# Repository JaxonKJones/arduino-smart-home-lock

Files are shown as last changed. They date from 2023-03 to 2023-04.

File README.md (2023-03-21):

# Project Description
This project was designed for home and apartment renters that want an affordable smart lock that is compliant with renter restrictions on changing locks (although anyone is welcome to use it). This is accomplished by utilizing existing lock hardware and keeping the keyed entry free for use. This design is compatible with most kinds of door locks and was made to be "plug and play." If modifications are needed, the source files included in this repository can be modified to fit your door. Assembly instructions are available through [instructables.com](https://www.instructables.com/) (project not yet released).

This smart lock uses an Arduino Nano as the microcontroller. It interfaces with a real time clock (the DS3231) to handle all scheduled events. The Nano also interfaces with a HC-05 Bluetooth module for users to program scheduled events, and manually engage or disengage the lock. The circuit is battery operated and uses a rechargeable 3.7v 18650 battery that is boosted to 5v. 

The smart lock is accessible/programmable via a bluetooth terminal smartphone app like the one **[here](https://play.google.com/store/apps/details?id=de.kai_morich.serial_bluetooth_terminal&hl=en_US&gl=US)**. Upon connecting and providing appropriate credentials, a menu will be displayed for the user allowing you to select several options. The major features are listed below:

## Modes:
Scheduling Mode: This option lets the user add, delete, or view existing schedules. When the desired schedules have been set the circuit enters into low power mode and can only be awoken by programmed interrupts on the DS3231 or the on board switch. This mode uses the least power at approximately 1 mAh. Using this mode gives the user the longest battery life with around 140 days before needing to be recharged.  

Bluetooth Mode: This mode uses the most power and is not recommended but is available for convenience if desired. This mode keeps the module paired, or open to pairing, so that the deadbolt can be locked or unlocked at any moment

Bluetooth Limited Mode: This mode combines the functionality of the previous two modes. The user defines a schedule for when the module should be on and pairable. This helps reduce unnecessary battery usage for time when the lock state is least likely to change (e.g. sleeping hours, working hours, school hours, etc.) 

## Quick Facts:
**Major Components:**
- Arduino Nano
- DS3231 Real Time Clock
- HC-05 Bluetooth Module 
- MG-90 Servo
- 18650 Battery
<!-- Total Project Time: ~40 hours -->
**Total project cost:** $25 (Market equivalents of this project cost ~$100+)  
See [Bill of Materials](#bill-of-materials)

**Battery Life**
140 day battery life in schedule mode°  
30 day battery life in Bluetooth limited mode*°  
*Based on a 3500 mAh 18650 battery
°Based on a 12 hour availability

# Bill of Materials
**NOTE:** Buying these components online usually means you'll need to purchase a pack or 2+. I'd recommend first looking for a local source if you don't have these components already. If a local supplier is unreasonable then [Temu](https://www.temu.com/) or [AliExpress](https://www.aliexpress.us/?gatewayAdapt=glo2usa&_randl_shipto=US) are your cheapsest options and [Amazon](https://www.amazon.com/) or [Ebay](https://www.ebay.com/) are your fastest options.
- [Arduino Nano](https://www.temu.com/type-c-usb-nano-3-0-with-bootloader-compatible-nano-3-0-controller-for-arduino-ch340-usb-driver-16mhz-original-ic-atmega328p-g-601099512651761.h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)
- [HC-05 Bluetooth Module](https://www.ebay.com/itm/364130886349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)
- [DS3231 Real Time Clock](https://www.amazon.com/DS3231-AT24C32-Module-Memory-Replace/dp/B09LLMYBM1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)
- [Portable Battery Pack](https://www.ebay.com/itm/255619278468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)** 
- [MG90 Servo](https://www.temu.com/mg90s-metal-gear-digital-9g-servo-for-rc-helicopter-plane-boat-car-mg90-9g-g-601099512694957.html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)  
**If you can afford it, I'd recommend spending a bit more money to purchase a nice battery. Many cheap batteries on the internet lie about their capacity and you'll severally limit the battery life of the smart lock if you get a bad battery - could just buy a [case](https://www.aliexpress.us/item/3256802714206963.html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) or [this one](https://www.amazon.com/Diymore-Battery-Shield-Raspberry-Arduino/dp/B0784FPF8J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) (An 18650 battery case if important because it has a built in charing circuit and boost converter) and then get the [battery](https://www.18650batterystore.com/products/samsung-35e-protected) separtely to ensure you get a good product
- 2x MOSFET
- SPST Switch
- Momentary Switch
- 2x 10k ohm resistors
- 1x 2k ohm resistor
- 1x 4k ohm resistor
- 2x 330 microFarad Capacitor
- PCB - see pcb under [Systems](#systems)

# Instructions
Work in progress. Will be posted on instructables.com
<!-- finish... -->

# Systems
## Code
All of the code for this project is located in a single file called 
**arduino_smart_home_lock_code.ino** located in the arduino_smart_home_lock folder. This single file will contain all the functions needed for the arduino nano. If you are curious, I encourage you to read through the code to become familiar with it. There are also variables you may change such as the password to access the lock via bluetooth.
<!-- finish... -->

## PCB
The schematic and PCB for this project was created in Eagle - a software produced by autodesk. The PCB folder contains both a schematic (for reference and hand soldering) and a PCB file that can be manufactured by companies such as [jlcpcb](https://jlcpcb.com/) if you'd like to have a board that is professionally made. 

## Mechanical
The case for this smart lock can be 3D printed using any home 3D printer. All tolerances for fits have been adjusted for the ender 3 v2 but should work on any printer with equal or higher printing accuracy. Several versions of the case are available in the STL folder.
<!-- finish... -->

# Disclaimer
<!-- finish... -->

# Acknowledgements
Special thanks to the following individuals for providing critical support and feedback to make this project a success:  
Jarom Christensen   -   PCB design  
Devin Bingham       -   PCB debugging  
Michael Davis       -   Feature suggestions and market valuation  
My Wife             -   Letting me use our kitchen table as my workbench for 3 weeks

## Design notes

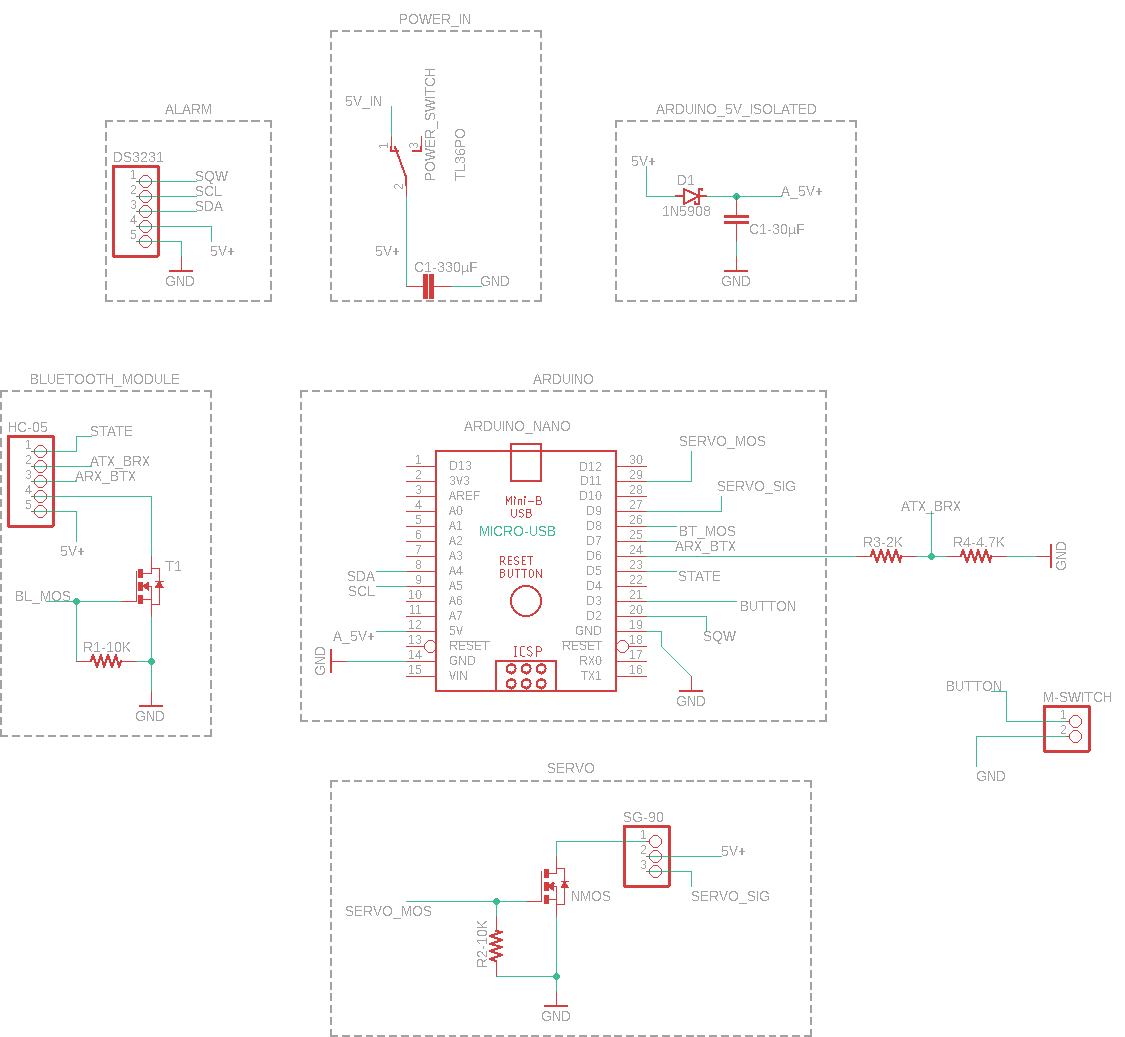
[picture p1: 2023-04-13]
Schematic and PCB/Wire Diagram.png

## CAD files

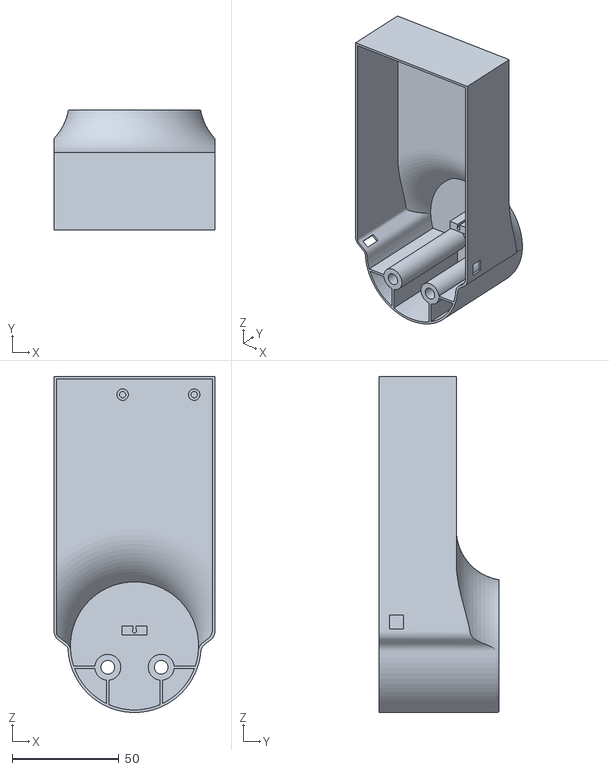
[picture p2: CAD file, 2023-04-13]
STL/Smart Home Lock Casing_Final - fully enclosed.stl
75.4 x 56.2 x 157.4

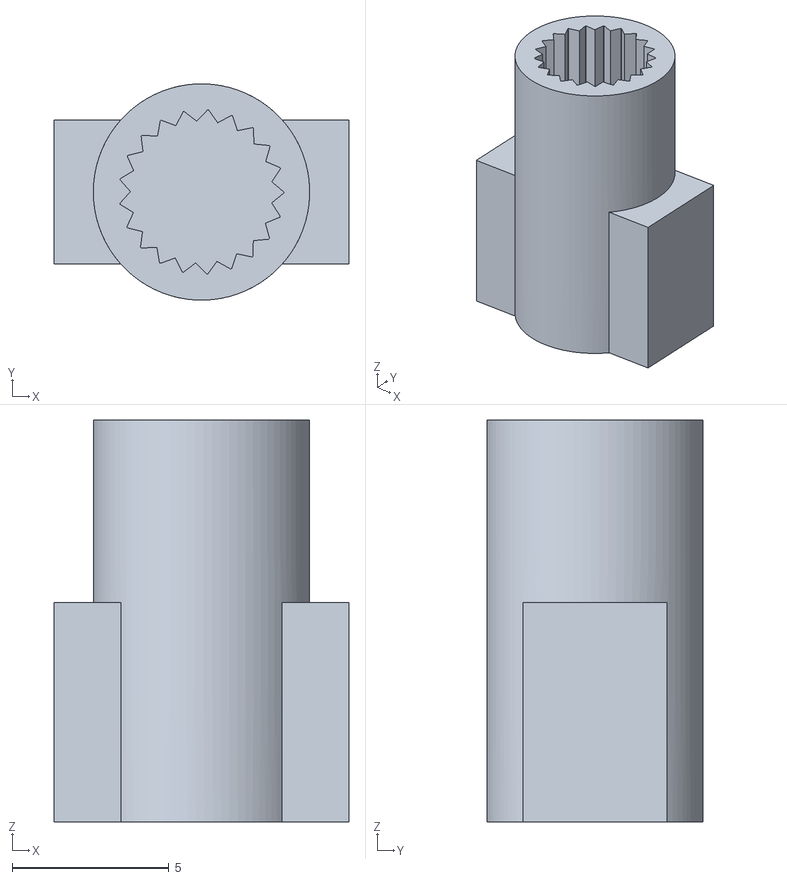
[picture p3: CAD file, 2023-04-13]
STL/SG90_Servo_Horn_Door_Lock.stl
9.40 x 6.90 x 12.8

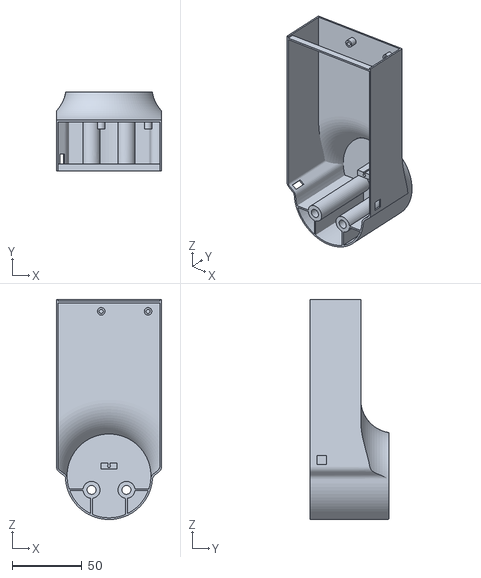
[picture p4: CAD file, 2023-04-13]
STL/Smart Home Lock Casing_Final - open top.stl
75.4 x 56.2 x 157.4

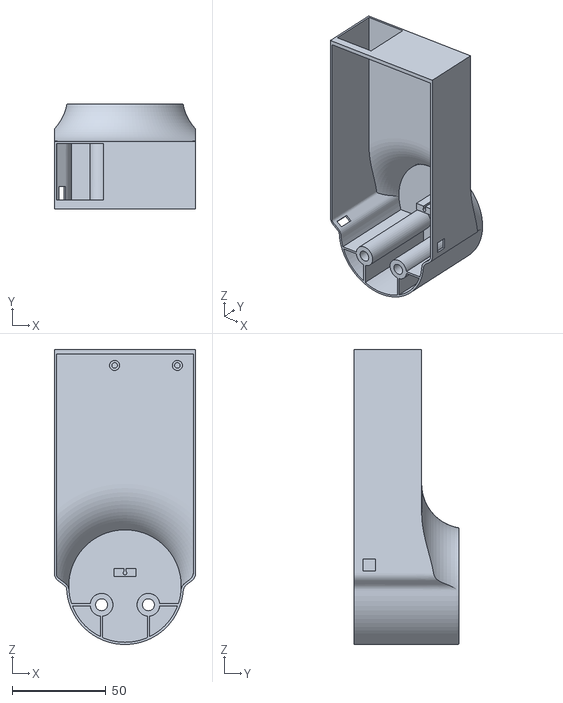
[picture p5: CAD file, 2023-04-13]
STL/Smart Home Lock Casing_Final - open battery port.stl
75.4 x 56.2 x 157.4

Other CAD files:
STL/SG90_Servo_Horn_Door_Lock.f3d
STL/Smart Home Lock Casing CAD.f3d

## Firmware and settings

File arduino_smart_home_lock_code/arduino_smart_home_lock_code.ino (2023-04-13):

#include <SoftwareSerial.h>
#include <avr/sleep.h>
#include <EEPROM.h>
#include <Wire.h>
#include "RTClib.h"
#include <Servo.h>


RTC_DS3231 rtc;
Servo lock;

#define STATE_PIN 5  // set state pin to pin 5
#define EN_PIN 4  // set enable pin to pin 4
#define BUTTON_PIN 3  // set button pin to pin 3
volatile bool fromButton = false;
volatile int buttonState = 0;
volatile long buttonCalls = 0;
#define ALARM_PIN 2 // interrupt pin from DS3231
#define BLUETOOTH_MOS 8 // mosfet for hc-05
#define SERVO 9 // pwm pin for servo
#define SERVO_MOS 11 // servo enable pin
SoftwareSerial BTserial(7, 6); // RX | TX

// User Variables
#define password "11235" //set your password here
#define verbose false //turn on when debugging from serial monitor, otherwise keep this false
#define TEST false //keep this false unless testing specific code in the test() function

// function declarations
void bprint(String arg);
void Fbprint(__FlashStringHelper* arg);
void auth();
int menu();
void pair(bool checkTimeOut);
void scheduler();
void save(char day, char h1, char h2, char m1, char m2, char state);
void del(int index);
char* load(bool print);
long nextEvent(char events[]);
void setAlarm(long);
void bluetoothMode();
void bluetoothLimited();
void scheduleMode();
void enterSleep();
void dev();
void servo(int state);
void vacationMode();
void buttonISR();
void alarmISR();


// setup function
void setup() { 
  // Serial Settings
  if(verbose) {
    Serial.begin(9600);
  }
  BTserial.begin(9600);
  Fbprint(F("Powering on..."));

  //rtc config
  Wire.begin();
  rtc.begin();
  // rtc.adjust(DateTime(F(__DATE__), F(__TIME__))); //Keep this commented out otherwise the RTC will reset anytime the arduino is powercycled
  pinMode(ALARM_PIN, INPUT_PULLUP);
  rtc.disableAlarm(1);
  rtc.disableAlarm(2);
  rtc.clearAlarm(1);
  rtc.clearAlarm(2);
  rtc.writeSqwPinMode(DS3231_OFF);
  rtc.disable32K();

  //servo config
  lock.attach(9);

  //pin config
  pinMode(STATE_PIN, INPUT);
  pinMode(BUTTON_PIN, INPUT_PULLUP);
  pinMode(BLUETOOTH_MOS, OUTPUT);
  digitalWrite(BLUETOOTH_MOS, HIGH);
  pinMode(EN_PIN, OUTPUT);
  digitalWrite(EN_PIN, LOW);
  pinMode(SERVO_MOS, OUTPUT);
  digitalWrite(SERVO_MOS, LOW);

  if(TEST == true){
    test();
  }

  //pair if not already connected
  if(digitalRead(STATE_PIN) == LOW){
    pair(true); // pair mode with timeout
  }
  auth();
}

// main loop
void loop() {
  int mode = menu();
  if (mode == '1'){
    //run scheduler
    scheduler();
  }
  if (mode == '2'){
    //run schedule mode
    scheduleMode();
  }
  else if (mode == '3'){
    //run bluetooth mode
    bluetoothMode();
  }
  else if (mode =='4'){
    //config bluetooth limited mode
    bluetoothLimited();
  }
  else if (mode == '5'){
    // run vacation mode
    vacationMode();
  }
  else if (mode == '6'){
    // run dev mode
    dev();
  }
}

void test(){
  Fbprint(F("Testing..."));
  // BTserial.print(F(\Testing...\n"));
  while(true){
    //test code here.
     char events[] = {'5', '1', '1', '1', '0', 'L','5', '1', '1', '1', '2', 'L','5', '1', '1', '1', '3', 'L','5', '1', '1', '1', '4', 'L', NULL};
    // char events[] = {'5', '1', '1', '0', '8', 'L'};
    long alarm = nextEvent(events);
    setAlarm(alarm);
    enterSleep();

    // delay(10000);
  }
}

// function definitions
void bprint(String arg) {
  if (verbose){
    Serial.println(arg);
  }
}

void Fbprint(__FlashStringHelper* arg) {
  if (verbose) {
    Serial.println(arg);
  }
}

void auth(){
  BTserial.print(F("\n-Home Lock-"));
  BTserial.print(F("\nEnter Password: "));
  long startTime = millis();
  // if user takes longer than 60s to enter password, it will go to scheduleMode
  while(true){
    if (BTserial.available()) {
      String input = BTserial.readString();
      delay(30);
      if (input == password){
        BTserial.print(F("\nAuthenticated..."));
        Fbprint(F("Authenticated..."));
        return;
      }
      else{
        BTserial.print(F("\nPassword Incorrect"));
      }
      // check to see if it has been 60s
      if (millis() - startTime > 60000){
        BTserial.print(F("\nTimed Out..."));
        scheduleMode();
      }
    }
  }
}

int menu(){
  if(digitalRead(STATE_PIN) == LOW){
    pair(false);
  }
  BTserial.print(F("\n\n-Main Menu-\n1: Scheduler\n2: Schedule Mode\n3: Bluetooth Mode\n4: Bluetooth Limited\n5: Vacation Mode\n6: Dev"));
  while(true){
    if (BTserial.available()) {
      char command = BTserial.read();
      if (command == '0') {
        return command;
      } 
      else if (command == '1') {
        return command;
      }
      else if (command == '2') {
        return command;
      }
      else if (command == '3') {
        return command;
      }
      else if (command == '4') {
        return command;
      }
      else if (command == '5') {
        return command;
      }
      else if (command == '6') {
        return command;
      }
      else if (command == '7') {
        return command;
      }
      else if (command == '8') {
        return command;
      }
      else if (command == '9') {
        return command;
      }
    }
    if (digitalRead(STATE_PIN) == LOW){
      pair(false);
    }
  }
    
}

void pair(bool checkTimeOut){
  Fbprint(F("Pairing..."));
  long startTime = millis();
  while(digitalRead(STATE_PIN) == LOW){
    delay(1000);
    if (checkTimeOut && millis() - startTime > 60000){
      Fbprint(F("Timed Out..."));
      scheduleMode();
      return;
    }
  } 
  Fbprint(F("Paired!"));
}

void scheduler(){  
  Fbprint(F("Scheduler"));
  BTserial.print(F("\n\n-Scheduler-"));
  BTserial.print(F("\n1:Add  2:Delete  3:See all Schedules   or Exit"));
  // format is d:hh:mm - ex: 1:12:00 is Sunday at 12:00
  while(true){
    if (BTserial.available()) {
      String input = BTserial.readString();
      delay(30);
      if (input == "0"){
        break;
      }
      else if (input == "1"){
        //Add schedule
        BTserial.print(F("\nEnter Schedule: (d-hh:mm-U/L) or Exit"));
        while(true){
          if (BTserial.available()){
            String input = BTserial.readString();
            delay(30);
            if (input == "0"){
              return;
            }
            else{
              bprint(input);
              if(strlen(input.c_str()) == 9){
                // Parse input to get hour, minute, and day of week
                char day = input.substring(0, 1).charAt(0);
                char h1 = input.substring(2, 3).charAt(0);
                char h2 = input.substring(3, 4).charAt(0);
                char m1 = input.substring(5, 6).charAt(0);
                char m2 = input.substring(6, 7).charAt(0);
                char state = input.substring(8, 9).charAt(0);
                //save schedule to EEPROM
                save(day, h1, h2, m1, m2, state);
                break;
              }
            }
          }
        }

      }
      else if(input == "2"){
        //Send schedules to BTserial
        load(true);
        BTserial.print(F("\nEnter Schedule index to Delete or Exit"));
        while(true){
          if (BTserial.available()){
            String input = BTserial.readString();
            delay(30);
            if (input == "0"){
              return;
            }
            else{
              bprint(input);
              if(strlen(input.c_str()) <= 2){
                // Parse input to get hour, minute, and day of week
                int index = input.toInt();
                //save schedule to EEPROM
                del(index-1);
                break;
              }
            }
          }
        }

        //Delete schedule
        

      }
      else if(input == "3"){
        //See all schedules
        load(true);
      }
      
    }
    if(digitalRead(STATE_PIN) == LOW){
      pair(false);
    }
  }
}

void save(char day, char h1, char h2, char m1, char m2, char state){
  //check eeprom to see where the next available slot is
  int address = 2; // index 0 reserved for number of schedules, index 1 reserved for next state (U/L)
  int saves = EEPROM.read(0);
  if (saves < 80){
    int i = saves*6+address;
    //save day
    EEPROM.write(i, day);
    bprint("var saved: " + String(day) + " to address: " + String(i) + " in eeprom");

    //save h1
    EEPROM.write(i + 1, h1);
    bprint("var saved: " + String(h1) + " to address: " + String(i + 1) + " in eeprom");

    //save h2
    EEPROM.write(i + 2, h2);
    bprint("var saved: " + String(h2) + " to address: " + String(i + 2) + " in eeprom");

    //save m1
    EEPROM.write(i + 3, m1);
    bprint("var saved: " + String(m1) + " to address: " + String(i + 3) + " in eeprom");

    //save m2
    EEPROM.write(i + 4, m2);
    bprint("var saved: " + String(m2) + " to address: " + String(i + 4) + " in eeprom");

    //save state
    EEPROM.write(i + 5, state);
    bprint("var saved: " + String(state) + " to address: " + String(i + 5) + " in eeprom");

    //increment number of schedules
    EEPROM.write(0, saves + 1);
    bprint("var saved: " + String(saves + 1) + " to address: " + String(0) + " in eeprom");

    BTserial.print(F("\nSaved!"));
  }
  else{
    BTserial.print(F("\nError: Max number of schedules reached!"));
  }
  
}

void del(int index){
  //go to index in eeprom
  int address = 2 + (index * 6);
  //delete schedule
  EEPROM.write(address, 0);
  EEPROM.write(address + 1, 0);
  EEPROM.write(address + 2, 0);
  EEPROM.write(address + 3, 0);
  EEPROM.write(address + 4, 0);
  EEPROM.write(address + 5, 0);
  //decrement number of schedules
  int saves = EEPROM.read(0);
  EEPROM.write(0, saves - 1);
  //move all schedules after index up
  for(int i = address; i < (saves * 6) + 1; i++){
    EEPROM.write(i, EEPROM.read(i + 6));
  }
  BTserial.print(F("\nSchedule Deleted!\n"));
}

char* load(bool print){
  int sched = EEPROM.read(0);
  int eventsLength = sched * 6 + 1;//add 1 for null terminator
  char *events = (char*)malloc(eventsLength * sizeof(char));
  if (print){
    BTserial.print(("\nSchedules: " + String(sched) + "\n").c_str());
    BTserial.print(F("#:   Day:    HH:   MM:   State:"));
    //print out all schedules from eeprom
    int address = 2;
    for(int i = 0; i < sched; i++){
      BTserial.print(("\n" + String(i+1) + ":     "+ String(char(EEPROM.read(address))) + "     " + String(char(EEPROM.read(address + 1))) + String(char(EEPROM.read(address + 2))) + "     " + String(char(EEPROM.read(address + 3))) + String(char(EEPROM.read(address + 4))) + "       " + String(char(EEPROM.read(address + 5))) + "").c_str());
      address += 6;
      }
    return NULL;
  }
  else{
    // load all schedules from eeprom
    for(int i = 0; i < eventsLength; i++){
      events[i] = char(EEPROM.read(i+2));
      // bprint("var loaded: " + String(events[i]) + " from address: " + String(i+2) + " in eeprom");
    }

    //add null as last element of events array
    events[eventsLength] = NULL;
    bprint(String(events));
    return events;
  }
}

long nextEvent(char events[]) {
  // get length of array
  int numEvents = EEPROM.read(0);
  bprint("Number of Events: " + String(numEvents));
  DateTime now = rtc.now();// get current date/time from RTC module
  long currentDOW = now.dayOfTheWeek();
  long currentHour = now.hour();
  long currentMinute = now.minute();
  long eventTime = 0;
  long closestEventTime = 0;
  char nextState;
  int eventIndex = NULL;
  String nextEvent = "";


  for (int i = 0, j = 0; i < numEvents; i++, j+=6, eventTime=0) { // i handles how many events and j handles characters in events 
    // get day of week, hour, minute, and state of event
    long eventDOW = (events[j] - '0');
    long eventHour = (events[j+1] - '0') * 10 + (events[j+2] - '0');
    long eventMinute = (events[j+3] - '0') * 10 + (events[j+4] - '0');
    char state = events[j+5];
    String event = String(eventDOW) + "-" + String(eventHour) + ":" + String(eventMinute) + "-" + String(state);

    // calculate time to midnight
    long timeToMidnight = (24L * 3600L) - (currentHour * 3600L + currentMinute * 60L); 
    
    if (eventDOW < currentDOW || (eventDOW == currentDOW && (eventHour < currentHour || (eventHour == currentHour && eventMinute < currentMinute)))) {
      // The event is in the past or next week
      eventTime = timeToMidnight + (eventDOW - currentDOW - 1) * 3600L*24L + eventHour * 3600L + eventMinute * 60L;
      eventTime += 3600L*24L*7L; // Add one week to the time
    }
    else if(eventDOW > currentDOW){
      // The event is in the future before the end of the week
      eventTime = timeToMidnight + (eventDOW - currentDOW - 1) * 3600L*24L + eventHour * 3600L + eventMinute * 60L;
    }
    else{
      // The event is in the future today
      eventTime = (eventHour - currentHour) * 3600L + (eventMinute - currentMinute) * 60L;
    }

    if(eventTime == 0){
      // event just occured, set to next week
      eventTime = 3600L*24L*7L;
    }

    if(closestEventTime == 0 || eventTime < closestEventTime) {
      closestEventTime = eventTime;
      nextState = state;
      eventIndex = i;
      nextEvent = event;

    }
  }
  bprint("Next Event: " + nextEvent);
  bprint("Time to event: " + String(closestEventTime) + " (" +String(float(closestEventTime)/float(3600L)) +" hours)");
  bprint("Next State: " + String(nextState));
  Serial.flush();
  
  EEPROM.write(1, nextState); // save next state to EEPROM index 1

  return closestEventTime;
}

void setAlarm(long timeToEvent) {
  bprint("Setting alarm for " + String(timeToEvent) + " seconds from now \n");
  Serial.flush();
  DateTime now = rtc.now();
  DateTime nextAlarm = DateTime(now.unixtime() + timeToEvent);
  rtc.setAlarm1(nextAlarm, DS3231_A1_Day); // See https://github.com/garrysblog/DS3231-Alarm-With-Adafruit-RTClib-Library for more info
}

void bluetoothMode(){
  Fbprint(F("Bluetooth Mode"));
  if(digitalRead(STATE_PIN) == LOW){
    pair(false);
  }
  BTserial.print(F("\n\n-Bluetooth Mode-"));
  BTserial.print(F("\n1: Lock Door\n2: Unlock Door\n or Exit"));
  while(true){
    if (BTserial.available()) {
      char command = BTserial.read();
      if (command == '1') {
        //lock door
        servo(1);
        BTserial.print(F("\nLocked!"));
      }
      else if (command == '2') {
        //unlock door
        servo(0);
        BTserial.print(F("\nUnlocked!"));
      }
      else if (command == '0') {
        //exit to main menu
        break;        
      }
    }
  }
}

void bluetoothLimited(){
  // Function is not complete
  return;

  BTserial.print(F("\n\n-Bluetooth Limited-"));
  BTserial.print(F("\n1: Run Bluetooth Limited  2: Set Daily Schedule or Exit to Main Menu"));
  while(true){
    if (BTserial.available()) {
      char command = BTserial.read();
      if (command == '0') {
        //exit to main menu
        break;        
      }
      else if (command == '1') {
        //run bluetooth limited
        
      }
      else if (command == '2') {
        //set hours for bluetooth module to be on each day 
        BTserial.print(F("\n-Format HH:MM HH:MM-")); //start hour and minute, end hour and minute
        BTserial.print(F("\n-Example 08:00 20:00-")); //start hour and minute, end hour and minute
        while(true){
          if (BTserial.available()) {
            String command = BTserial.readString();
            if (command == '0') {
              //exit to main menu
              return;        
            }
            else{
              // parse command for start and end time
              char starth1 = command.substring(0,1).charAt(0);
              char starth2 = command.substring(1,2).charAt(0);
              char startm1 = command.substring(3,4).charAt(0);
              char startm2 = command.substring(4,5).charAt(0);
              char endh1 = command.substring(6,7).charAt(0);
              char endh2 = command.substring(7,8).charAt(0);
              char endm1 = command.substring(9,10).charAt(0);
              char endm2 = command.substring(10,11).charAt(0);

              // save start and end time to EEPROM - start at index 500
              EEPROM.write(500, starth1);
              EEPROM.write(501, starth2);
              EEPROM.write(502, startm1);
              EEPROM.write(503, startm2);
              EEPROM.write(504, endh1);
              EEPROM.write(505, endh2);
              EEPROM.write(506, endm1);
              EEPROM.write(507, endm2);
            }
          }
        }
        

      }
    }
  }
}

void scheduleMode(){
  Fbprint(F("Schedule Mode"));
  BTserial.print(F("\n\n-Schedule Mode Active-"));
  BTserial.print(F("\nBluetooth will deactivate but can be awoken using the on system switch..."));
  delay(500); //wait for bluetooth to send message
  digitalWrite(BLUETOOTH_MOS, LOW); //turn off bluetooth module
  int saves = EEPROM.read(0);
  while(saves != 0){
    char* events = load(false);    
    setAlarm(nextEvent(events));
    free(events);
    fromButton = false;
    enterSleep();
    bprint("fromButton: " + String(fromButton));
    //determine if alarm or button interrupt woke up
    if(fromButton == false){
    //interrupt came from alarm
      char state = char(EEPROM.read(1));
      bprint("State: " + String(state));
      Serial.flush();
      if(state == 'U'){
        servo(0);
        buttonState = 1;
      }
      else if(state == 'L'){
        servo(1);
        buttonState = 0;
      }
      delay(60000); //NOTE: temporary fix for alarm repeating - will disable lock for 1 minute
    }
    if(fromButton == true){
      if (buttonState == 0){
        buttonState = 1;
        servo(0);
      }
      else{
        buttonState = 0;
        servo(1);
      }
    }
  }

  //Otherwise, no events set - so sleep CPU
  sleep_enable();                       // Enabling sleep mode
  set_sleep_mode(SLEEP_MODE_PWR_DOWN);  // Setting the sleep mode, in this case full sleep
  noInterrupts();                       // Disable interrupts
  attachInterrupt(digitalPinToInterrupt(BUTTON_PIN), buttonISR, LOW);
  interrupts();                         // Allow interrupts again
  sleep_cpu();
}

void enterSleep(){
  //turn off hc-05
  
  sleep_enable();                       // Enabling sleep mode
  set_sleep_mode(SLEEP_MODE_PWR_DOWN);  // Setting the sleep mode, in this case full sleep
  
  noInterrupts();                       // Disable interrupts
  attachInterrupt(digitalPinToInterrupt(ALARM_PIN), alarmISR, LOW);
  attachInterrupt(digitalPinToInterrupt(BUTTON_PIN), buttonISR, LOW);
  interrupts();                         // Allow interrupts again
  Fbprint(F("Sleeping..."));
  Serial.flush();
  sleep_cpu();                          // Enter sleep mode
  Fbprint(F("Awake..."));

  /* The program will continue from here when it wakes */
  
  // Disable and clear alarm
  rtc.disableAlarm(1);
  rtc.clearAlarm(1);
}

void dev(){
  Fbprint(F("Dev Mode"));
  BTserial.print(F("\n\n-DEBUG-"));
  BTserial.print(F("\n1: Set RTC\n2: RTC Info\n3:Reset EEPROM\nOr Exit"));
  while(true){
    if (BTserial.available()) {
      char input = BTserial.read();
      delay(30);
      if (input == '0'){
        break;
      }
      else if (input == '1'){
        set_rtc();
      }
      else if(input == '2'){
        DateTime now = rtc.now();
        float temp = rtc.getTemperature();
        BTserial.print(("\n" + String(now.day()) + "  " + String(now.hour()) + ":" + String(now.minute()) + "     Temp: " + String(temp).c_str()));
        bprint("RTC Info: " + String(now.day()) + "  " + String(now.hour()) + ":" + String(now.minute()) + "    Temp: " + String(temp).c_str());
      }
      else if(input == '3'){
        EEPROM.write(0, 0);
        for (int i = 1 ; i < EEPROM.length() ; i++) {
          EEPROM.write(i, NULL);
        }
        BTserial.print(F("\nEEPROM Reset\n"));
        Fbprint(F("EEPROM Reset"));
      }
      else if(input == '4'){
        for (int i = 0 ; i < EEPROM.length() ; i++) {
          // Serial.print(String(char(EEPROM.read(i))) + " ");
          bprint(String(char(EEPROM.read(i))) + " ");
        }
      }
    }
  }
}

void servo(int state){
  if(state == 0){
    //unlock door
    digitalWrite(SERVO_MOS, HIGH);
    delay(50);
    lock.write(140);
    Fbprint(F("Door Unlocked"));
    delay(500);
    digitalWrite(SERVO_MOS, LOW);
  }
  else if(state == 1){
    //lock door
    digitalWrite(SERVO_MOS, HIGH);
    delay(50);
    lock.write(30);
    Fbprint(F("Door Locked"));
    delay(500);
    digitalWrite(SERVO_MOS, LOW);
  }
}

void vacationMode(){
  //turn off the bluetooth module and do not look for alarms
  Fbprint(F("Vacation Mode"));
  BTserial.print(F("\n\n-Vacation Mode Active-"));
  BTserial.print(F("\nBluetooth will deactivate but can be awoken using the on system switch..."));
  delay(2000); //wait for bluetooth to send message
  digitalWrite(BLUETOOTH_MOS, LOW); //turn off bluetooth module
  while(true){
    //sleep the cpu
    sleep_enable();                       // Enabling sleep mode
    set_sleep_mode(SLEEP_MODE_PWR_DOWN);  // Setting the sleep mode, in this case full sleep
    
    noInterrupts();                       // Disable interrupts     
    attachInterrupt(digitalPinToInterrupt(BUTTON_PIN), buttonISR, LOW);
    interrupts();                         // Allow interrupts again
    sleep_cpu();                          // Enter sleep mode

    //allow button operation only
    if(fromButton == true){
      if (buttonState == 0){
        buttonState = 1;
        servo(0);
      }
      else{
        buttonState = 0;
        servo(1);
      }
      fromButton = false;
      delay(1000);
    }
  }
}
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

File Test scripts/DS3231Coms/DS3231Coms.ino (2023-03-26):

#include <Wire.h>
#include "RTClib.h"
#include <avr/sleep.h>  // AVR library for controlling the sleep modes
#include <EEPROM.h>

RTC_DS3231 rtc;

#define ALARM_PIN 2

void setup() {
  Serial.begin(9600);
  Wire.begin();
  rtc.begin();
  // uncomment the following line to set the time and date for the first time
  rtc.adjust(DateTime(F(__DATE__), F(__TIME__)));
  pinMode(ALARM_PIN, INPUT_PULLUP);
  Serial.println(""); // buffer
  Serial.print("Current Time: ");
  Serial.print(rtc.now().dayOfTheWeek());
  Serial.print("-");
  Serial.print(rtc.now().hour());
  Serial.print(":");
  Serial.println(rtc.now().minute());

  rtc.disableAlarm(1);
  rtc.disableAlarm(2);
  rtc.clearAlarm(1);
  rtc.clearAlarm(2);

  rtc.writeSqwPinMode(DS3231_OFF);

}

// function declarations
long nextEvent(char events[]);
void setAlarm(long timeToEvent);
void enterSleep();
void alarmISR();

// main loop
void loop() {
  char events[] = {'5', '1', '1', '1', '0', 'L','5', '1', '1', '1', '2', 'L','5', '1', '1', '1', '3', 'L','5', '1', '1', '1', '4', 'L', NULL};
  // char events[] = {'5', '1', '1', '0', '8', 'L'};
  long alarm = nextEvent(events);
  setAlarm(alarm);
  enterSleep();
  // DOW();
  // delay(100000);

  
}


// function definitions
long nextEvent(char events[]) {
  // get length of array
  int numEvents = 0;
  for (int i = 0; events[i] != NULL; i++) {
    numEvents++;
  }
  numEvents = numEvents/6;
  Serial.print("Number of Events: ");
  Serial.println(numEvents);
  DateTime now = rtc.now();// get current date/time from RTC module
  long currentDOW = now.dayOfTheWeek();
  long currentHour = now.hour();
  long currentMinute = now.minute();
  long eventTime = 0;
  long closestEventTime = 0;
  char nextState;
  int eventIndex = NULL;
  String nextEvent = "";


  for (int i = 0, j = 0; i < numEvents; i++, j+=6, eventTime=0) { // i handles how many events and j handles characters in events 
    // get day of week, hour, minute, and state of event
    long eventDOW = (events[j] - '0');
    long eventHour = (events[j+1] - '0') * 10 + (events[j+2] - '0');
    long eventMinute = (events[j+3] - '0') * 10 + (events[j+4] - '0');
    char state = events[j+5];
    String event = String(eventDOW) + "-" + String(eventHour) + ":" + String(eventMinute) + ":" + String(state);

    // calculate time to midnight
    long timeToMidnight = (24L * 3600L) - (currentHour * 3600L + currentMinute * 60L); 
    
    // Serial.print("Event: " + event);
    
    if (eventDOW < currentDOW || (eventDOW == currentDOW && (eventHour < currentHour || (eventHour == currentHour && eventMinute < currentMinute)))) {
      // The event is in the past or next week
      eventTime = timeToMidnight + (eventDOW - currentDOW - 1) * 3600L*24L + eventHour * 3600L + eventMinute * 60L;
      eventTime += 3600L*24L*7L; // Add one week to the time
    }
    else if(eventDOW > currentDOW){
      // The event is in the future before the end of the week
      eventTime = timeToMidnight + (eventDOW - currentDOW - 1) * 3600L*24L + eventHour * 3600L + eventMinute * 60L;
    }
    else{
      // The event is in the future today
      eventTime = (eventHour - currentHour) * 3600L + (eventMinute - currentMinute) * 60L;
    }
    // Serial.print("Time to Event: ");
    // Serial.println(eventTime);

    if (closestEventTime == 0 || eventTime < closestEventTime) {
      closestEventTime = eventTime;
      nextState = state;
      eventIndex = i;
      nextEvent = event;

    }
    // delay(2000);
  }
  Serial.println("");
  Serial.println("Next Event: " + nextEvent);
  Serial.println("Time to event: " + String(closestEventTime) + " (" +String(float(closestEventTime)/float(3600L)) +" hours)");
  Serial.println("Next State: " + String(nextState));
  Serial.flush();
  EEPROM.write(1, nextState); // save next state to EEPROM index 1

  return closestEventTime;
}


void setAlarm(long timeToEvent) {
  DateTime now = rtc.now();
  DateTime nextAlarm = now.unixtime() + timeToEvent;
  rtc.setAlarm1(nextAlarm, DS3231_A1_Minute);
}

void enterSleep(){
  sleep_enable();                       // Enabling sleep mode
  set_sleep_mode(SLEEP_MODE_PWR_DOWN);  // Setting the sleep mode, in this case full sleep
  
  noInterrupts();                       // Disable interrupts
  attachInterrupt(digitalPinToInterrupt(ALARM_PIN), alarmISR, LOW);
  Serial.println("Going to sleep!");
  Serial.flush(); 
  interrupts();                         // Allow interrupts again
  sleep_cpu();                          // Enter sleep mode

  /* The program will continue from here when it wakes */
  
  // Disable and clear alarm
  rtc.disableAlarm(1);
  rtc.clearAlarm(1);
}

void alarmISR() {
  sleep_disable(); // Disable sleep mode
  detachInterrupt(digitalPinToInterrupt(ALARM_PIN)); // Detach the interrupt to stop it firing
  // This function is called when the alarm goes off
  Serial.println("Alarm triggered!");
  // read state from eeprom index 1
  char state = EEPROM.read(1);
  Serial.print("State: ");
  Serial.println(state);
}


void setSchedule() {
  int saves = 0;
  char state = 'W';
  char events[] = {'1', '0', '7', '4', '0', 'L',
                 '2', '0', '7', '4', '0', 'L',
                 '3', '0', '7', '4', '0', 'L',
                 '4', '0', '7', '4', '0', 'L',
                 '5', '0', '7', '4', '0', 'L',
                 '0', '0', '7', '2', '0', 'U',
                 '1', '0', '7', '2', '0', 'U',
                 '2', '0', '7', '2', '0', 'U',
                 '3', '0', '7', '2', '0', 'U',
                 '4', '0', '7', '2', '0', 'U',
                 '5', '0', '7', '2', '0', 'U',
                 '1', '1', '5', '2', '0', 'U',
                 '2', '1', '0', '2', '0', 'U',
                 '3', '1', '6', '2', '0', 'U',
                 '4', '1', '0', '2', '0', 'U',
                 '5', '1', '0', '2', '0', 'U',
                 '0', '2', '3', '3', '0', 'L',
                 '1', '2', '3', '3', '0', 'L',
                 '2', '2', '3', '3', '0', 'L',
                 '3', '2', '3', '3', '0', 'L',
                 '4', '2', '3', '3', '0', 'L',
                 '5', '2', '3', '3', '0', 'L',
                 '6', '2', '3', '3', '0', 'L',  
    };
    //save events to eeprom
    for (int i = 2; i < sizeof(events)+2; i++) {
      EEPROM.write(i, events[i]);
      saves++;
    }
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

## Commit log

2023-03-03 working DS3231 interrupt on coms.ino
2023-03-03 working interrupt, alarm, and time calculations
2023-03-12 added button ISR and debounce. Fixed pins
    [DS3231Coms.ino, lockTesting.ino, smart_home_lock.ino]
2023-03-21 STL for case - no top
    [Smart Home Lock Casing_Final - no top.stl]
2023-03-21 Fixed button interrupt, updated readme.md
    [arduino_smart_home_lock_code.ino]
2023-03-24 Alarm debug started, adding verbose print
2023-04-13 fixed button state in schedule mode
    [arduino_smart_home_lock_code.ino]
2023-04-13 added sch files
    [Arduino_Smart_Home_Lock.sch]
2023-04-13 renamed PCB folder
2023-04-13 added CAD files
    [Smart Home Lock Casing CAD.f3d, Smart Home Lock Casing_Final - fully enclosed.stl, Smart Home Lock Casing_Final - no top.stl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]
2023-04-13 added servo horn files
    [SG90_Servo_Horn_Door_Lock.f3d, SG90_Servo_Horn_Door_Lock.stl]
2026-02-26 Update project description in README
    Removed link to assembly instructions on Instructables.
